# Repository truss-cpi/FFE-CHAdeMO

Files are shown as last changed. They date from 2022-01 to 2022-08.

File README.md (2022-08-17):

# FFE-CHAdeMO
Code and info for after-market CHAdeMO modifications to the Ford Focus Electric

The data provided has not been vetted or officially validated in any way. It is provided with no warranty and is used entirely at your own risk. 

High Voltage DC can easily maim or kill and should only be worked on by appropriately trained professionals.

You assume all responsibility if you damage anything or hurt/kill anyone using this code or information - and you agree that the creator of this repository will not be held liable in any way.

Remember: Not only will this kill you, it will hurt the whole time you're dying.

UPDATE:
A redesign of the control circuit is under way using parts that are more readily attainable and that do not require surface mount soldering. The ADM3052 is getting replaced by an MCP2561 High Speed CAN Transceiver, with SFH636 High Speed (1MBit) Optocouplers carrying the CAN0 Rx/Tx between the two isolated sections of the shield. These couplers are good for 2MHz switching frequency and the 500kbit data rate we're using should only need half that.

Validation is in progress with a "test" version of the shield code that can verify inputs/outputs, relay control and CAN transmission.

It should be noted that if the CAN1RX pin (DAC0) is not pulled up to 3.3V during validation testing, the CAN1TX pin (53) will not output test data reliably.

Also, the lowest CANBus data rate supported by the Arduino Due is 40kbit. Seen other lower values noted elsewhere but that seems to be the lowest value required by the CANBus spec and is the lowest that gave output when set on the Due.

New schematics to follow soon followed by a new board layout.

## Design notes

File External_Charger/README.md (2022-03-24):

The code in this folder controls a CHAdeMO Fast Charger interface, allowing multiple on-board charger modules (SOBDMs) to provide battery level DC output in parallel.

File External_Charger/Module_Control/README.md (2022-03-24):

This code generates CANBus frames that simulate module outputs the SOBDM expects to see during operation.

The module requires the vehicle to be in a specific state to go into charge mode and these data points are used to confirm that state.

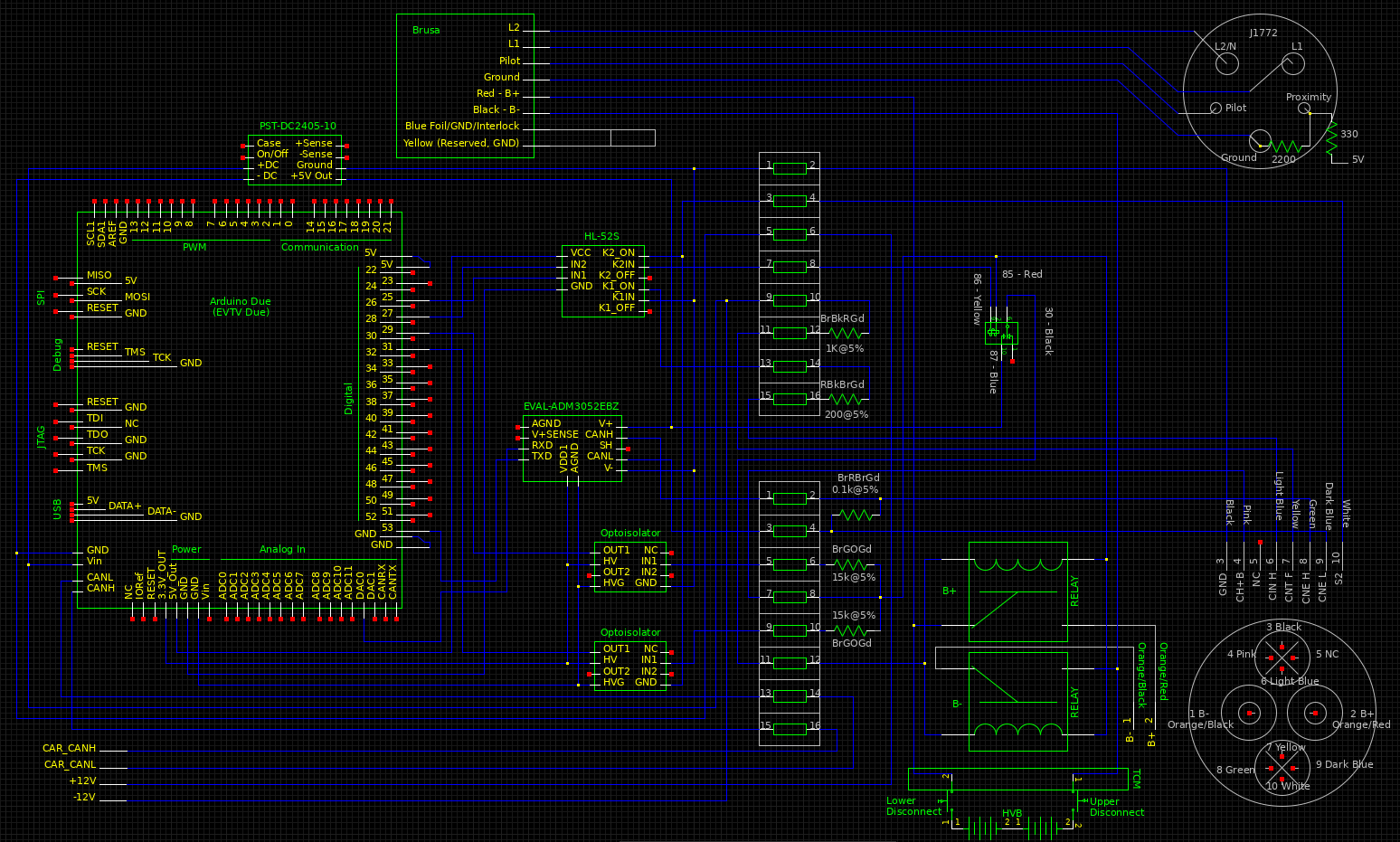
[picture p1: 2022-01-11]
Schematic Overview.png

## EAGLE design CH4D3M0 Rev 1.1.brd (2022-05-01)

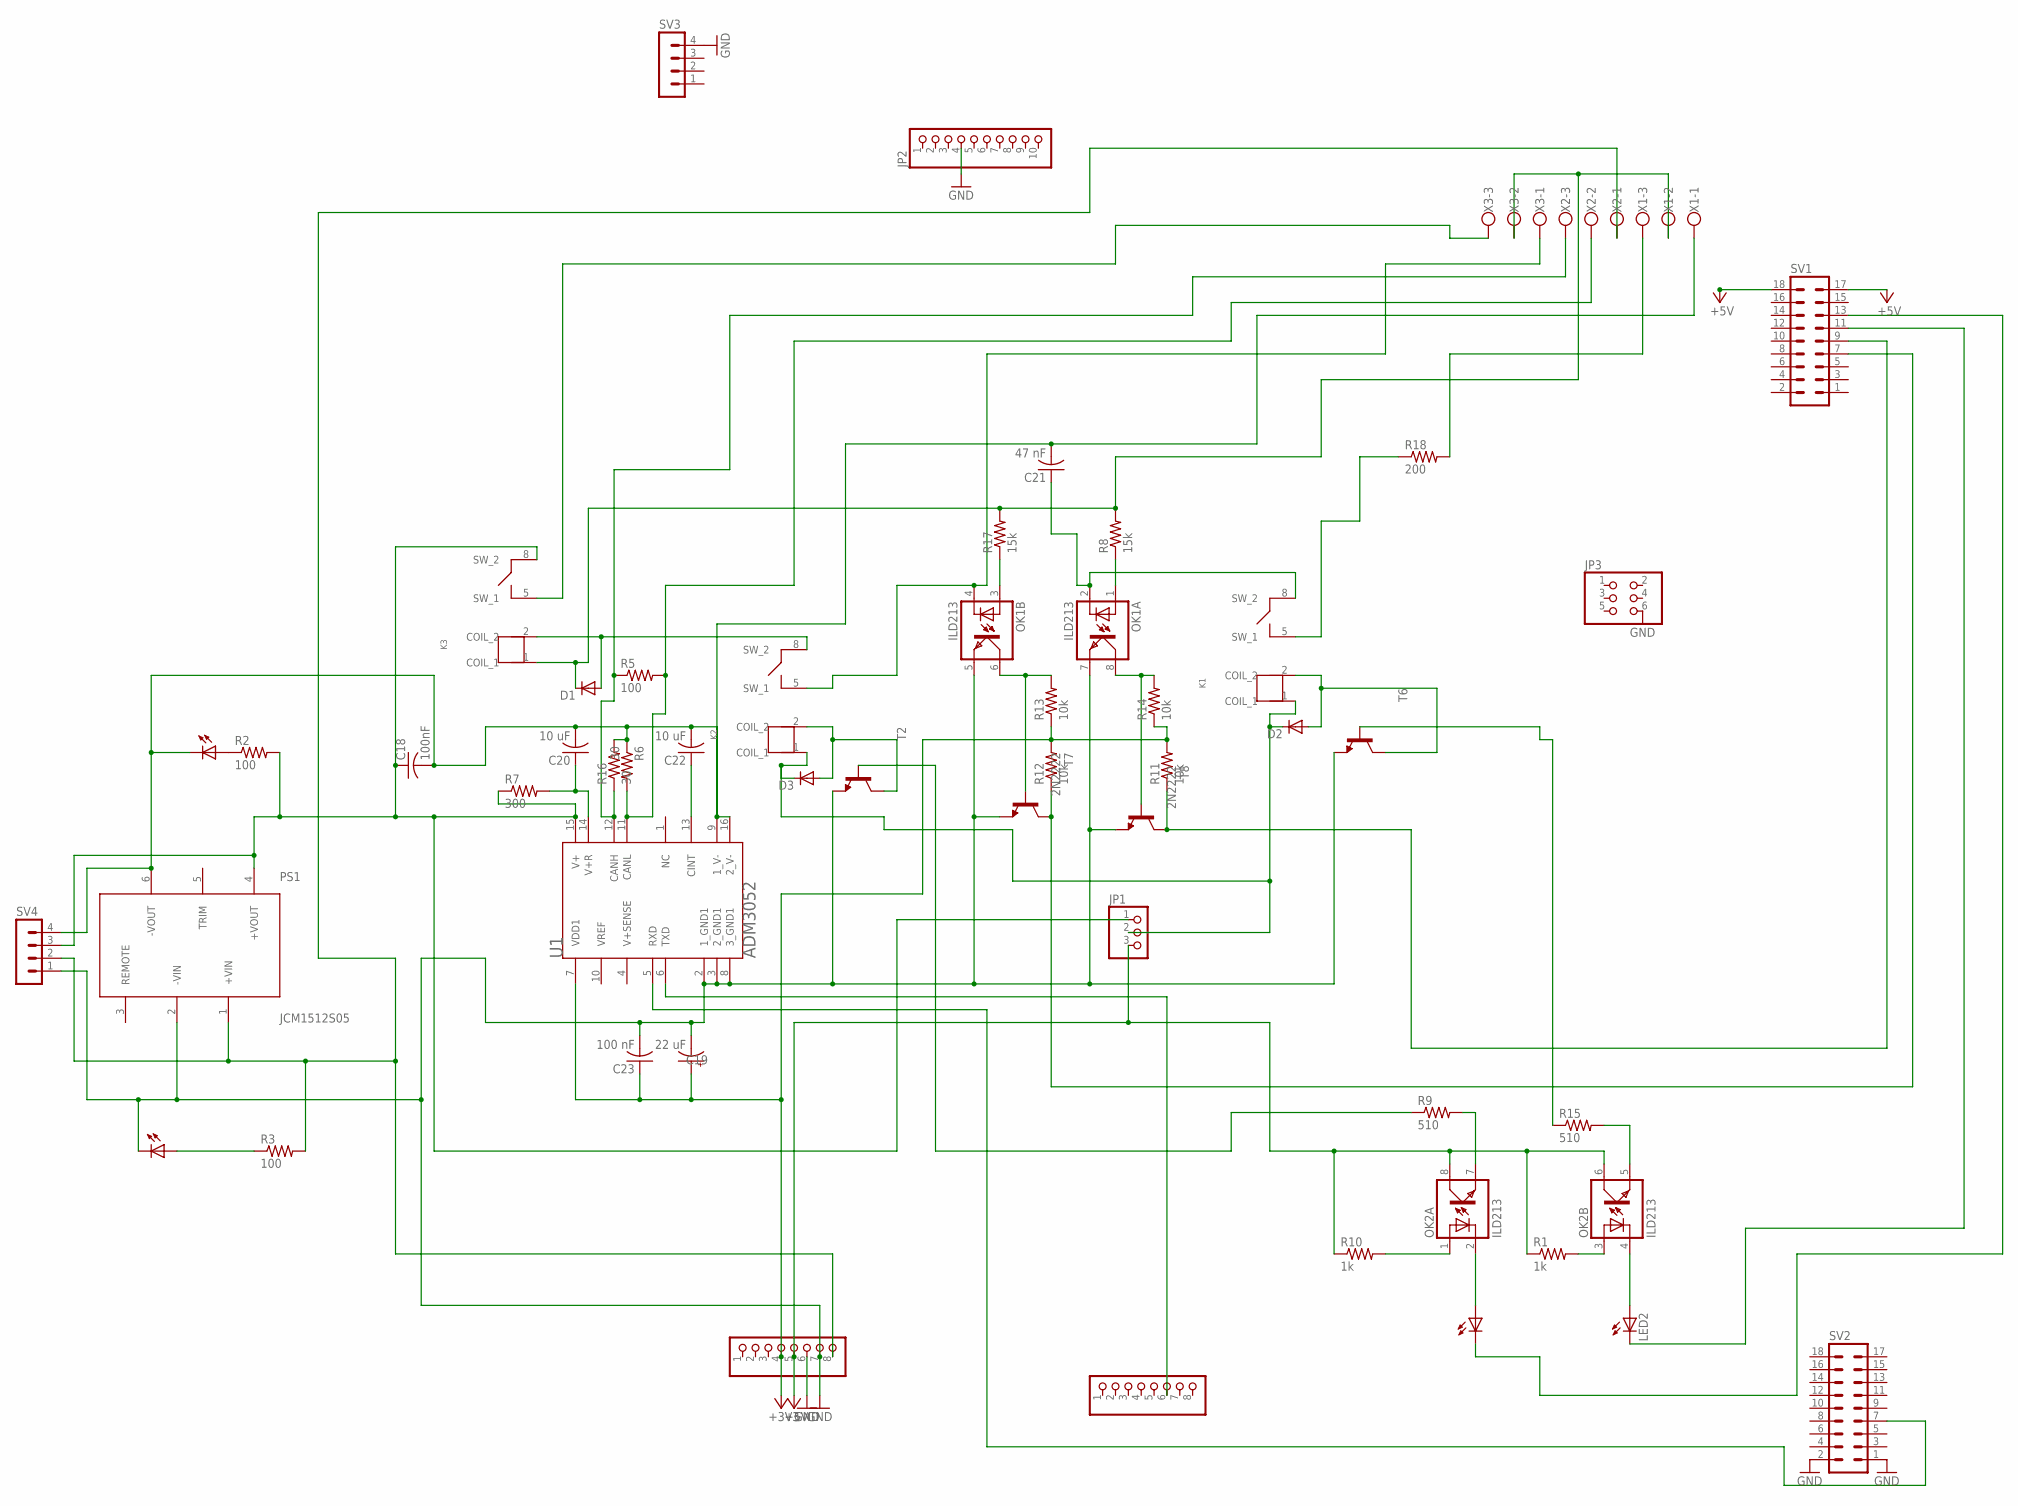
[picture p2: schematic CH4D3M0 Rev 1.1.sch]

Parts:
ADCH, ADCH2: PINHD-1X8; 1X08
C18: 100nF; C025-024X044
C19: 22 uF; E2,5RE
C20, C22: 10 uF; C025-024X044
C21: 47 nF; C025-024X044
C23: 100 nF; C025-024X044
D1, D2, D3: DIODE-D-5; D-5
JP1: PINHD-1X3; 1X03
JP2: PINHD-1X10; 1X10
JP3: PINHD-2X3; 2X03
K1, K2, K3: G6DN-1ATHROUGH_HOLE; G6DN-1A
LED1, LED2, LED3, LED4: LED_ELD260; LED_LD260
OK1, OK2: ILD213; SOIC08
PS1: JCM1512S05; JCMXX
R1, R10: 1k; 0204/7
R2, R3, R5: 100; 0204/7
R6, R16: 30; 0204/7
R7: 300; 0204/7
R8, R17: 15k; 0204/7
R9, R15: 510; 0204/7
R11, R12, R13, R14: 10k; 0204/7
R18: 200; 0204/7
SV1, SV2: MA09-2
SV3, SV4: MA04-1
T2, T6: BC547-NPN-TO92-CBE; TO92-CBE
T7, T8: 2N2222; TO92-EBC-OVAL
U1: ANALOG_DEVICES_INC_ADM3052ANALOG_DEVICES_INC_ADM3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; ANALOG_DEVICES_INC_ADM3052_0
X1, X2, X3: W237-103

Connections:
+3V3: ADCH2.4, C19.+, C23.1, R11.2, R12.2, R13.1, R14.1, U1.7 (VDD1)
+5V: ADCH2.5, JP1.3, OK2.6 (COL), OK2.8 (COL), R1.1, R10.1, SV1.17, SV1.18
GND: ADCH2.6, ADCH2.7, C19.-, C23.2, JP2.4, JP3.6, LED4.K (C), OK1.5 (EMIT), OK1.7 (EMIT), PS1.2 (-VIN), SV2.1, SV2.2, SV3.4, SV4.1, T2.E, T6.E, T7.E, T8.E, U1.2 (1_GND1), U1.3 (2_GND1), U1.8 (3_GND1)
unnamed: D2.C, D3.C, JP1.2, K1.1 (COIL_1), K2.1 (COIL_1)
unnamed: C18.1, JP1.1, K3.8 (SW_2), PS1.4 (+VOUT), R2.2, R7.1, SV4.3, U1.15 (V+)
unnamed: C20.1, R7.2, U1.14 (V+R)
unnamed: C22.1, U1.13 (CINT)
unnamed: K3.5 (SW_1), X3.3
unnamed: R18.2, X1.3
unnamed: C18.2, C20.2, C21.2, C22.2, LED3.K (C), PS1.6 (-VOUT), R6.1, R16.2, SV4.4, U1.9 (1_V-), U1.16 (2_V-), X1.1
unnamed: R5.2, R6.2, U1.11 (CANL), X2.2
unnamed: C21.1, K1.8 (SW_2), OK1.2 (C)
unnamed: K1.5 (SW_1), R18.1
unnamed: D1.C, K3.1 (COIL_1), R8.2, R17.2, X1.2, X3.2
unnamed: OK1.1 (A), R8.1
unnamed: OK1.3 (A), R17.1
unnamed: ADCH2.8, PS1.1 (+VIN), R3.2, SV4.2, X2.1
unnamed: D1.A, K2.8 (SW_2), K3.2 (COIL_2)
unnamed: K2.5 (SW_1), OK1.4 (C), X3.1
unnamed: OK1.6 (COL), R13.2, T7.B
unnamed: OK1.8 (COL), R14.2, T8.B
unnamed: R12.1, SV1.7, T7.C
unnamed: ADCH.6, U1.6 (TXD)
unnamed: R11.1, SV1.9, T8.C
unnamed: SV2.7, U1.5 (RXD)
unnamed: D2.A, K1.2 (COIL_2), T6.C
unnamed: D3.A, K2.2 (COIL_2), T2.C
unnamed: OK2.7 (EMIT), R9.2
unnamed: LED1.A, OK2.2 (C)
unnamed: OK2.1 (A), R10.2
unnamed: OK2.3 (A), R1.2
unnamed: R9.1, T2.B
unnamed: LED1.K (C), SV1.13
unnamed: R15.1, T6.B
unnamed: OK2.5 (EMIT), R15.2
unnamed: LED2.A, OK2.4 (C)
unnamed: LED2.K (C), SV1.11
unnamed: R5.1, R16.1, U1.12 (CANH), X2.3
unnamed: LED3.A, R2.1
unnamed: LED4.A, R3.1

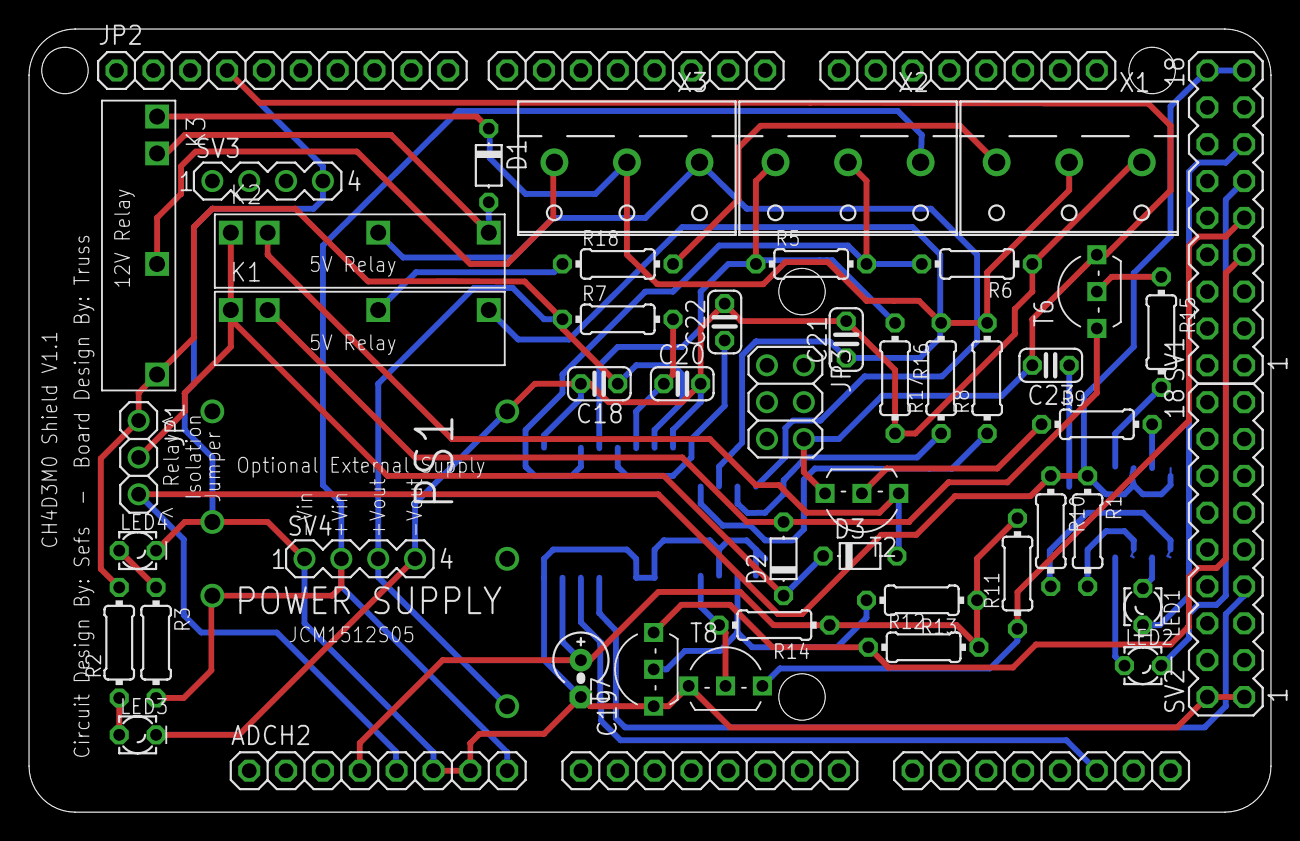
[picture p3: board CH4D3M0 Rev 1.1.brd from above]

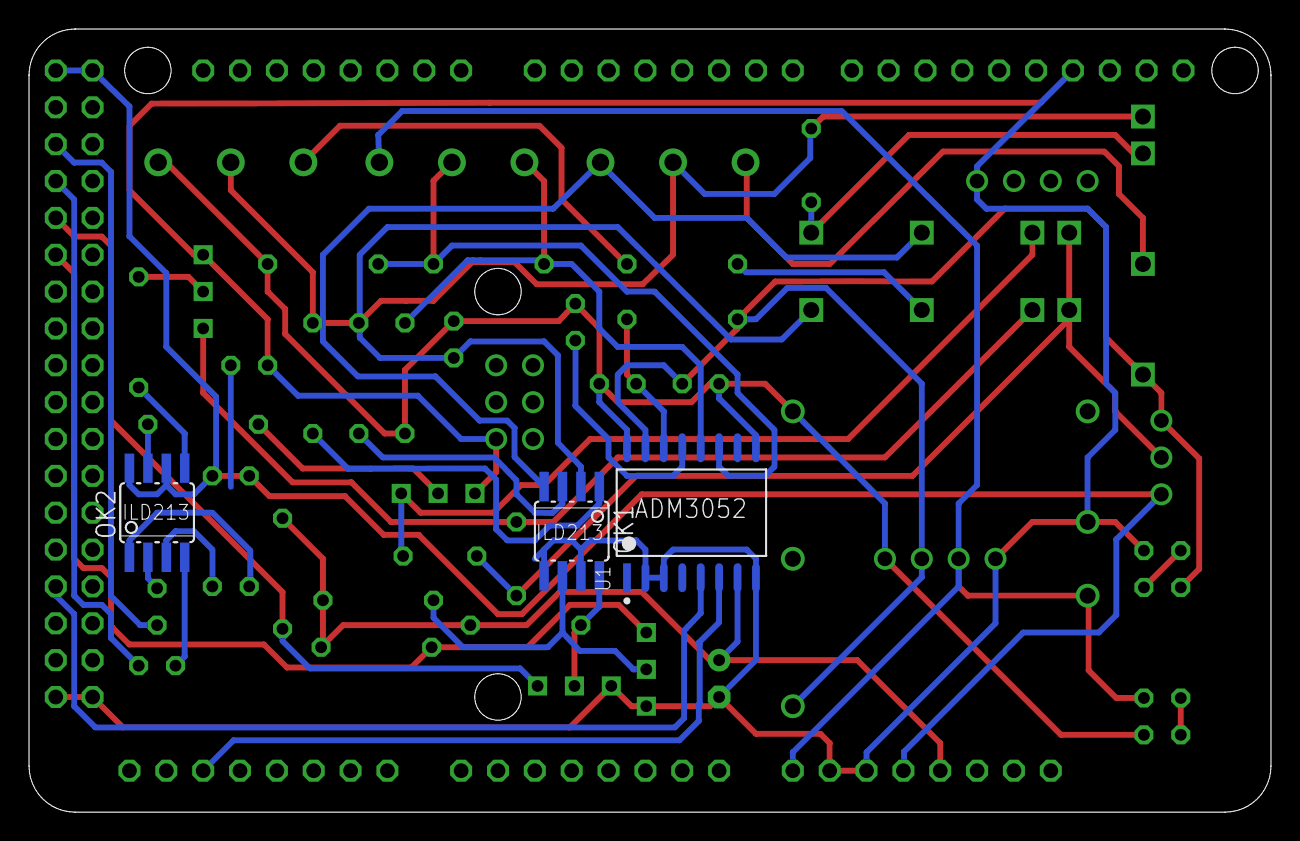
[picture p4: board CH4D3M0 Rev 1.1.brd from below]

Board: 2 copper layers, 85.6 x 54.0 mm, 56 parts (3 on the bottom side), 40 nets.

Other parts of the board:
ADCL: 1X08
COMMUNICATION: 1X08
PWML: 1X08

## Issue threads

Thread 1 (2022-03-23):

Sorry I'm didn't know where I can text you either...

Elan-II, 2022-03-23:
Last half year I'm looking for way to start ford fusion/focus/c-max electric on board 3.3 kWt charger, but I'm have only charger, not entire car. I'm working on EV conversion and repair service, and would like to ask some of your can logs, become you somehow find that 0x7E2 asks charger some status. I can give you al information about other chargers, that I'm turn on instead, if needed this.

Elan-II, 2022-03-23:
Because, not become...

Elan-II, 2022-03-24:
Can you give me link where you get that original code?

truss-cpi, 2022-03-24:
There is no original link. This was pursued as a personal project by the original author and the software was given to me when I purchased the hardware - as he did not wish to pursue development of it. I've posted it as open source so that others may use it. What you see IS the original code, with the exception of me cleaning up some formatting and adding more verbose comments.

There is other separate code I have not had a chance to look at that was used to control SOBDMs outside the vehicle, so they could be "stacked" together to act as a fast charger. There may be something of use in there. I'll try to get it posted to the main branch soon.

truss-cpi, 2022-03-24:
[https://github.com/truss-cpi/FFE-CHAdeMO/blob/main/External_Charger/Module_Control/sodbm_controller.ino](https://github.com/truss-cpi/FFE-CHAdeMO/blob/main/External_Charger/Module_Control/sodbm_controller.ino) should have what you're looking for. It has several loops that simulate the output of frames the SOBDM expects to see on the bus.

Elan-II, 2022-03-25:
As I'm see, it arduino project, can't you somehow add some strings like
Serial.print (received CAN id);
Serial.print (received CAN data[i];
And make some logs for me, while car chargings. I can pay you for this.

Closed 2022-03-24.

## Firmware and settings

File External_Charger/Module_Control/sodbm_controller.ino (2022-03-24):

#include <SPI.h>
#include <Arduino.h>
#include <due_can.h>
#include <due_wire.h>
#include "variant.h"
#include <Wire_EEPROM.h>
#include <Scheduler.h>
#include <elapsedMillis.h>

elapsedMillis timeElapsed;
elapsedMillis lrx;

#define Serial SerialUSB
template<class T> inline Print &operator <<(Print &obj, T arg) {
  obj.print(arg);  //Sets up Serial streaming Serial<<someshit;
  return obj;
}

class Field {
  public:
    uint16_t msb;
    uint16_t bits;
    uint32_t data;
    char* fieldName;
};

class Msg {
  public:
    char* moduleName;
    uint16_t msgID;
    uint64_t msg;
    Field fields[16];
    uint8_t field_count;
};

class StringTable {
  public:
    Msg messages[32];
};

class EEPROMvariables {
  public:
    uint8_t CANdo;        //Use Serial port if 2, CAN0 if 0 or CAN1 if 1
    char logfile[80];
    uint16_t transmitime = 0;
    boolean logger;
    uint32_t datarate = 500000;
    uint8_t goodEEPROM;
    CAN_FRAME outFrame;

};

StringTable stringTable;
EEPROMvariables myVars;
uint16_t page = 475;
uint16_t dummy;
char cmdBuffer[100];
char logstring[200];
char logstring2[300] = "";
char logstringt[200];
char logstringtl[200];
char logstringt1[200];
char logstringc1[200];
char logstringts[200];
char msgBuff[100];
float Version = 1.10;
int ptrBuffer;
short logcycle = 0;
boolean handlingEvent, debug;
int b1167 = 0x70;
int b142D = 0x02;
int reportedvolts = 0;
int reportedvoltspre = 0;
int tempA = 0;
int tempAint = 0;
int tempB = 0;
int tempBint = 0;
int tempC = 0;
int tempCint = 0;
int VACint = 0;
int AACint = 0;
int contcommand = 0;
float reportedamps = 0;
int VACint1 = 0;
int VACint2 = 0;
int reportvolts1 = 0;
int reportvolts2 = 0;
unsigned int timeout = 1000;

unsigned int incra = 1048575;
int chargevolts = 0;
float chargeamps = 0;
float battvolts = 333;
int chargevoltsint1 = 0;
int chargevoltsint2 = 0;
int chargecontrolint6 = 0;
int chargecontrolint7 = 0;
int chargeampsint = 0;
int battvoltsint = 0;
int reportedampsint = 0;



float acc = 0;
float pilot = 0;
float ampacity = 0;
float VAC = 0;
float AAC = 0;
float Hz = 0;
int sodbmdiagcycle = 1;
boolean sodbmreset = false;
int sodbmtoggle = 1;
int b207A = 0;
int b307A = 0;
int chargingstate=0;
int chargerStatus = 0;

CAN_FRAME inFrame;

void setup() {

  Wire.begin();
  Serial.begin(115200);

  EEPROM.setWPPin(19);
  EEPROM.read(page, myVars);
  if (myVars.goodEEPROM != 200)defaults();
  myVars.logger = false;


  initializeCAN();




  Scheduler.startLoop(ActiveDiagLoop);
  Scheduler.startLoop(StaticSimulatorLoop100ms);
  Scheduler.startLoop(StaticSimulatorLoop50ms);
  Scheduler.startLoop(StaticSimulatorLoop40ms);
  Scheduler.startLoop(OdometerSimulatorLoop);
  Scheduler.startLoop(GearShiftSimulatorLoop);
  Scheduler.startLoop(BECMStatusLoop);
  Scheduler.startLoop(SODBMControlLoop);
  Scheduler.startLoop(BECMVoltageLoop);
  Scheduler.startLoop(SysTimeSimulatorLoop);
  
  



}



void loop()
{
  while (SerialUSB.available()) {
    serialEvent();
  }
  sprintf(logstringtl, "%02X%02X", chargevoltsint1, chargevoltsint2);
  chargevolts = (float)strtol(logstringtl, NULL, 16);
  Serial<<"CV = ";
  Serial<<chargevolts;
  Serial<<" V          CC = ";
  Serial<<chargeampsint;
  Serial<<" A          Batt = ";
  Serial<<battvolts;
  Serial<<" V          AmpsOut = "; 
  Serial<<reportedamps;
  Serial<<" A          State = ";
  Serial<<chargingstate;
  Serial<<"\n"; 
  Serial<<"TempA = ";
  Serial<<tempA;
  Serial<<"     TempB = ";
  Serial<<tempB;
  Serial<<"     Temp C = ";
  Serial<<tempC;
  Serial<<"     Status = ";
  Serial<<chargerStatus;
  Serial<<"\n";
  
      reportedvolts = (reportedvoltspre & 0x1FF);
      reportedvolts = reportedvolts * 2;
      battvolts = reportedvolts/2;
      b207A = (reportedvolts & 0xFF00);
      b207A = b207A >> 8;
      b307A = (reportedvolts & 0x00FF);
    if (timeElapsed > timeout)
    {
      b1167 = 0x70;
      b142D = 0x02;
      chargingstate=0;
      chargeampsint = 0x00;
      chargevoltsint1 = 0x00;
      chargevoltsint2 = 0x00;
      chargecontrolint6 = 0x00;
      chargecontrolint7 = 0x00;
      contcommand = 0;
    }
    
    if (lrx > timeout)
    {
      pilot = 0;
        AAC = 0;
        VAC = 0;
        ampacity = 0;
        Hz = 0;
        tempAint = 0;
        tempA = 0;
        tempBint = 0;
        tempB = 0;
        tempCint = 0;
        tempC = 0;
    }


    myVars.outFrame.id = 0x105;
    myVars.outFrame.data.bytes[0] = reportvolts1;
    myVars.outFrame.data.bytes[1] = reportvolts2;
    myVars.outFrame.data.bytes[2] = reportedampsint;
    myVars.outFrame.data.bytes[3] = 0x00;
    myVars.outFrame.data.bytes[4] = 0x00;
    myVars.outFrame.data.bytes[5] = 0x00;
    myVars.outFrame.data.bytes[6] = 0x00;
    myVars.outFrame.data.bytes[7] = chargerStatus;
    sendCAN(myVars.CANdo);
    delay(40);
    myVars.outFrame.id = 0x109;
    myVars.outFrame.data.bytes[0] = VACint1;
    myVars.outFrame.data.bytes[1] = VACint2;
    myVars.outFrame.data.bytes[2] = AACint;
    myVars.outFrame.data.bytes[3] = 0x00;
    myVars.outFrame.data.bytes[4] = 0x00;
    myVars.outFrame.data.bytes[5] = tempAint;
    myVars.outFrame.data.bytes[6] = tempBint;
    myVars.outFrame.data.bytes[7] = tempCint;
    sendCAN(myVars.CANdo);

  /*
  sprintf(logstring2, "%.2f;%.2f;%.2f;%.2f;%.2f;%.2f;%.2f;%.2f;%.2f;%.2f;%.2f;%.2f;%.2f;%.2f;%.2f;%.2f;%.2f;%.2f;%.2f;%.2f;%.2f;%.2f;%.2f;%.2f;%.2f;%.2f;\n",
          batchadspl, hbattchar, hbattcoolin, mcon, hbattcurr, hbattvolt, ETE, hbatttemp, seqf,
          chacurrentf, torquedelivered, brakemode, estchatimef, motorRPM, MPH, throttle, brake, pwrt, acc, hvac, VAC, AAC, ampacity, Hz, mincell, maxcell);
  Serial << logstring2;
*/
  delay(60);
}

void ActiveDiagLoop()
{
  if (sodbmreset == true)
  {
    myVars.outFrame.id = 0x7E2;
    myVars.outFrame.data.bytes[0] = 0x04;
    myVars.outFrame.data.bytes[1] = 0x14;
    myVars.outFrame.data.bytes[2] = 0xFF;
    myVars.outFrame.data.bytes[3] = 0xFF;
    myVars.outFrame.data.bytes[4] = 0xFF;
    myVars.outFrame.data.bytes[5] = 0x00;
    myVars.outFrame.data.bytes[6] = 0x00;
    myVars.outFrame.data.bytes[7] = 0x00;
    myVars.outFrame.length = 8;
    myVars.outFrame.fid = 0;
    myVars.outFrame.rtr = 1;
    myVars.outFrame.priority = 0;
    myVars.outFrame.extended = false;
    Can0.sendFrame(myVars.outFrame);
  }




  sodbmdiagcycle =  sodbmdiagcycle * sodbmtoggle;

  if (sodbmdiagcycle == 1)
  {
    //SODBM Diagnostic Request for AC Voltage
    myVars.outFrame.id = 0x7E2;
    myVars.outFrame.data.bytes[0] = 0x03;
    myVars.outFrame.data.bytes[1] = 0x22;
    myVars.outFrame.data.bytes[2] = 0x48;
    myVars.outFrame.data.bytes[3] = 0x5E;
    myVars.outFrame.data.bytes[4] = 0x00;
    myVars.outFrame.data.bytes[5] = 0x00;
    myVars.outFrame.data.bytes[6] = 0x00;
    myVars.outFrame.data.bytes[7] = 0x00;
    myVars.outFrame.length = 8;
    myVars.outFrame.fid = 0;
    myVars.outFrame.rtr = 1;
    myVars.outFrame.priority = 0;
    myVars.outFrame.extended = false;
    Can0.sendFrame(myVars.outFrame);

  }

  else if (sodbmdiagcycle == 2)
  {
    //SODBM Diagnostic Request for AC Amps
    myVars.outFrame.id = 0x7E2;
    myVars.outFrame.data.bytes[0] = 0x03;
    myVars.outFrame.data.bytes[1] = 0x22;
    myVars.outFrame.data.bytes[2] = 0x48;
    myVars.outFrame.data.bytes[3] = 0x5F;
    myVars.outFrame.data.bytes[4] = 0x00;
    myVars.outFrame.data.bytes[5] = 0x00;
    myVars.outFrame.data.bytes[6] = 0x00;
    myVars.outFrame.data.bytes[7] = 0x00;
    myVars.outFrame.length = 8;
    myVars.outFrame.fid = 0;
    myVars.outFrame.rtr = 1;
    myVars.outFrame.priority = 0;
    myVars.outFrame.extended = false;
    Can0.sendFrame(myVars.outFrame);

  }

  else if (sodbmdiagcycle == 3)
  {
    //SODBM Diagnostic Request for Temp A
    myVars.outFrame.id = 0x7E2;
    myVars.outFrame.data.bytes[0] = 0x03;
    myVars.outFrame.data.bytes[1] = 0x22;
    myVars.outFrame.data.bytes[2] = 0xD1;
    myVars.outFrame.data.bytes[3] = 0x17;
    myVars.outFrame.data.bytes[4] = 0x00;
    myVars.outFrame.data.bytes[5] = 0x00;
    myVars.outFrame.data.bytes[6] = 0x00;
    myVars.outFrame.data.bytes[7] = 0x00;
    myVars.outFrame.length = 8;
    myVars.outFrame.fid = 0;
    myVars.outFrame.rtr = 1;
    myVars.outFrame.priority = 0;
    myVars.outFrame.extended = false;
    Can0.sendFrame(myVars.outFrame);

  }

  else if (sodbmdiagcycle == 4)
  {
    //SODBM Diagnostic Request for Temp B
    myVars.outFrame.id = 0x7E2;
    myVars.outFrame.data.bytes[0] = 0x03;
    myVars.outFrame.data.bytes[1] = 0x22;
    myVars.outFrame.data.bytes[2] = 0xD0;
    myVars.outFrame.data.bytes[3] = 0x0B;
    myVars.outFrame.data.bytes[4] = 0x00;
    myVars.outFrame.data.bytes[5] = 0x00;
    myVars.outFrame.data.bytes[6] = 0x00;
    myVars.outFrame.data.bytes[7] = 0x00;
    myVars.outFrame.length = 8;
    myVars.outFrame.fid = 0;
    myVars.outFrame.rtr = 1;
    myVars.outFrame.priority = 0;
    myVars.outFrame.extended = false;
    Can0.sendFrame(myVars.outFrame);

  }
  
    else if (sodbmdiagcycle == 5)
  {
    //SODBM Diagnostic Request for Temp C
    myVars.outFrame.id = 0x7E2;
    myVars.outFrame.data.bytes[0] = 0x03;
    myVars.outFrame.data.bytes[1] = 0x22;
    myVars.outFrame.data.bytes[2] = 0xD0;
    myVars.outFrame.data.bytes[3] = 0x0C;
    myVars.outFrame.data.bytes[4] = 0x00;
    myVars.outFrame.data.bytes[5] = 0x00;
    myVars.outFrame.data.bytes[6] = 0x00;
    myVars.outFrame.data.bytes[7] = 0x00;
    myVars.outFrame.length = 8;
    myVars.outFrame.fid = 0;
    myVars.outFrame.rtr = 1;
    myVars.outFrame.priority = 0;
    myVars.outFrame.extended = false;
    Can0.sendFrame(myVars.outFrame);

  }
  
  else if (sodbmdiagcycle == 6)
  {
    //SODBM Diagnostic Request for Status
    myVars.outFrame.id = 0x7E2;
    myVars.outFrame.data.bytes[0] = 0x03;
    myVars.outFrame.data.bytes[1] = 0x22;
    myVars.outFrame.data.bytes[2] = 0x48;
    myVars.outFrame.data.bytes[3] = 0x4F;
    myVars.outFrame.data.bytes[4] = 0x00;
    myVars.outFrame.data.bytes[5] = 0x00;
    myVars.outFrame.data.bytes[6] = 0x00;
    myVars.outFrame.data.bytes[7] = 0x00;
    myVars.outFrame.length = 8;
    myVars.outFrame.fid = 0;
    myVars.outFrame.rtr = 1;
    myVars.outFrame.priority = 0;
    myVars.outFrame.extended = false;
    Can0.sendFrame(myVars.outFrame);

  }
  delay(30);
}

void StaticSimulatorLoop100ms()
{
    //Exterior Temperature Message (100 ms)
    myVars.outFrame.id = 0x178;
    myVars.outFrame.data.bytes[0] = 0xC1;
    myVars.outFrame.data.bytes[1] = 0x2D;
    myVars.outFrame.data.bytes[2] = 0x00;
    myVars.outFrame.data.bytes[3] = 0x00;
    myVars.outFrame.data.bytes[4] = 0x8E;
    myVars.outFrame.data.bytes[5] = 0x4D;
    myVars.outFrame.data.bytes[6] = 0xB6;
    myVars.outFrame.data.bytes[7] = 0x4D;
    myVars.outFrame.length = 8;
    myVars.outFrame.fid = 0;
    myVars.outFrame.rtr = 1;
    myVars.outFrame.priority = 0;
    myVars.outFrame.extended = false;
    Can0.sendFrame(myVars.outFrame);
    
    delay(45);
    
    //Charger's DC/DC converter command Disable (100 ms)
    myVars.outFrame.id = 0x42D;
    myVars.outFrame.data.bytes[0] = 0x00;
    myVars.outFrame.data.bytes[1] = b142D; //0x02 before charge, 0x42 on charge
    myVars.outFrame.data.bytes[2] = 0x4D;
    myVars.outFrame.data.bytes[3] = 0x00;
    myVars.outFrame.data.bytes[4] = 0x46;
    myVars.outFrame.data.bytes[5] = 0x00;
    myVars.outFrame.data.bytes[6] = 0x00;
    myVars.outFrame.data.bytes[7] = 0x00;
    myVars.outFrame.length = 8;
    myVars.outFrame.fid = 0;
    myVars.outFrame.rtr = 1;
    myVars.outFrame.priority = 0;
    myVars.outFrame.extended = false;
    Can0.sendFrame(myVars.outFrame);
    delay(45);
}


void StaticSimulatorLoop50ms()
{
    //DC/DC Converter Low Voltage Set Point (50 ms)
    myVars.outFrame.id = 0x43E;
    myVars.outFrame.data.bytes[0] = 0x00;
    myVars.outFrame.data.bytes[1] = 0xA1;
    myVars.outFrame.data.bytes[2] = 0x00;
    myVars.outFrame.data.bytes[3] = 0x00;
    myVars.outFrame.data.bytes[4] = 0x00;
    myVars.outFrame.data.bytes[5] = 0x00;
    myVars.outFrame.data.bytes[6] = 0x00;
    myVars.outFrame.data.bytes[7] = 0x00;
    myVars.outFrame.length = 8;
    myVars.outFrame.fid = 0;
    myVars.outFrame.rtr = 1;
    myVars.outFrame.priority = 0;
    myVars.outFrame.extended = false;
    Can0.sendFrame(myVars.outFrame);
    delay(13);
    
    //DC/DC Converter Main Status (50 ms)
    myVars.outFrame.id = 0x43D;
    myVars.outFrame.data.bytes[0] = 0x43;
    myVars.outFrame.data.bytes[1] = 0x0F;
    myVars.outFrame.data.bytes[2] = 0x91;
    myVars.outFrame.data.bytes[3] = 0x19;
    myVars.outFrame.data.bytes[4] = 0x08;
    myVars.outFrame.data.bytes[5] = 0x94;
    myVars.outFrame.data.bytes[6] = 0x02;
    myVars.outFrame.data.bytes[7] = 0xA9;
    myVars.outFrame.length = 8;
    myVars.outFrame.fid = 0;
    myVars.outFrame.rtr = 1;
    myVars.outFrame.priority = 0;
    myVars.outFrame.extended = false;
    Can0.sendFrame(myVars.outFrame);
    delay(13);
    
    //Some PCM/ECM BS (50 ms)
    myVars.outFrame.id = 0x43E;
    myVars.outFrame.data.bytes[0] = 0x00;
    myVars.outFrame.data.bytes[1] = 0xA1;
    myVars.outFrame.data.bytes[2] = 0x00;
    myVars.outFrame.data.bytes[3] = 0x00;
    myVars.outFrame.data.bytes[4] = 0x00;
    myVars.outFrame.data.bytes[5] = 0x00;
    myVars.outFrame.data.bytes[6] = 0x00;
    myVars.outFrame.data.bytes[7] = 0x00;
    myVars.outFrame.length = 8;
    myVars.outFrame.fid = 0;
    myVars.outFrame.rtr = 1;
    myVars.outFrame.priority = 0;
    myVars.outFrame.extended = false;
    Can0.sendFrame(myVars.outFrame);
    delay(13);
}


void StaticSimulatorLoop40ms()
{
  //Main ECU Voltage Supply (40 ms)
    myVars.outFrame.id = 0x242;
    myVars.outFrame.data.bytes[0] = 0x04;//static
    myVars.outFrame.data.bytes[1] = 0xD0;//static
    myVars.outFrame.data.bytes[2] = 0x20;//static
    myVars.outFrame.data.bytes[3] = 0x0C;//static
    myVars.outFrame.data.bytes[4] = 0xE9;//static
    myVars.outFrame.data.bytes[5] = 0x28;
    myVars.outFrame.data.bytes[6] = 0x04;
    myVars.outFrame.data.bytes[7] = 0x01;
    myVars.outFrame.length = 8;
    myVars.outFrame.fid = 0;
    myVars.outFrame.rtr = 1;
    myVars.outFrame.priority = 0;
    myVars.outFrame.extended = false;
    Can0.sendFrame(myVars.outFrame);
    delay(35);
    
    myVars.outFrame.id = 0x242;
    myVars.outFrame.data.bytes[0] = 0x04;//static
    myVars.outFrame.data.bytes[1] = 0xD0;//static
    myVars.outFrame.data.bytes[2] = 0x20;//static
    myVars.outFrame.data.bytes[3] = 0x0C;//static
    myVars.outFrame.data.bytes[4] = 0xE9;//static
    myVars.outFrame.data.bytes[5] = 0x28;
    myVars.outFrame.data.bytes[6] = 0x00;
    myVars.outFrame.data.bytes[7] = 0x00;
    myVars.outFrame.length = 8;
    myVars.outFrame.fid = 0;
    myVars.outFrame.rtr = 1;
    myVars.outFrame.priority = 0;
    myVars.outFrame.extended = false;
    Can0.sendFrame(myVars.outFrame);
    delay(35);
    
    myVars.outFrame.id = 0x242;
    myVars.outFrame.data.bytes[0] = 0x04;//static
    myVars.outFrame.data.bytes[1] = 0xD0;//static
    myVars.outFrame.data.bytes[2] = 0x20;//static
    myVars.outFrame.data.bytes[3] = 0x0C;//static
    myVars.outFrame.data.bytes[4] = 0xE9;//static
    myVars.outFrame.data.bytes[5] = 0x2C;
    myVars.outFrame.data.bytes[6] = 0x05;
    myVars.outFrame.data.bytes[7] = 0x01;
    myVars.outFrame.length = 8;
    myVars.outFrame.fid = 0;
    myVars.outFrame.rtr = 1;
    myVars.outFrame.priority = 0;
    myVars.outFrame.extended = false;
    Can0.sendFrame(myVars.outFrame);
    delay(35);
    
    myVars.outFrame.id = 0x242;
    myVars.outFrame.data.bytes[0] = 0x04;//static
    myVars.outFrame.data.bytes[1] = 0xD0;//static
    myVars.outFrame.data.bytes[2] = 0x20;//static
    myVars.outFrame.data.bytes[3] = 0x0C;//static
    myVars.outFrame.data.bytes[4] = 0xE9;//static
    myVars.outFrame.data.bytes[5] = 0x28;
    myVars.outFrame.data.bytes[6] = 0x00;
    myVars.outFrame.data.bytes[7] = 0x00;
    myVars.outFrame.length = 8;
    myVars.outFrame.fid = 0;
    myVars.outFrame.rtr = 1;
    myVars.outFrame.priority = 0;
    myVars.outFrame.extended = false;
    Can0.sendFrame(myVars.outFrame);
    delay(35);
    
    myVars.outFrame.id = 0x242;
    myVars.outFrame.data.bytes[0] = 0x04;//static
    myVars.outFrame.data.bytes[1] = 0xD0;//static
    myVars.outFrame.data.bytes[2] = 0x20;//static
    myVars.outFrame.data.bytes[3] = 0x0C;//static
    myVars.outFrame.data.bytes[4] = 0xE9;//static
    myVars.outFrame.data.bytes[5] = 0x28;
    myVars.outFrame.data.bytes[6] = 0x04;
    myVars.outFrame.data.bytes[7] = 0x01;
    myVars.outFrame.length = 8;
    myVars.outFrame.fid = 0;
    myVars.outFrame.rtr = 1;
    myVars.outFrame.priority = 0;
    myVars.outFrame.extended = false;
    Can0.sendFrame(myVars.outFrame);
    delay(35);
    
    myVars.outFrame.id = 0x242;
    myVars.outFrame.data.bytes[0] = 0x04;//static
    myVars.outFrame.data.bytes[1] = 0xD0;//static
    myVars.outFrame.data.bytes[2] = 0x20;//static
    myVars.outFrame.data.bytes[3] = 0x0C;//static
    myVars.outFrame.data.bytes[4] = 0xE9;//static
    myVars.outFrame.data.bytes[5] = 0x2C;
    myVars.outFrame.data.bytes[6] = 0x02;
    myVars.outFrame.data.bytes[7] = 0x00;
    myVars.outFrame.length = 8;
    myVars.outFrame.fid = 0;
    myVars.outFrame.rtr = 1;
    myVars.outFrame.priority = 0;
    myVars.outFrame.extended = false;
    Can0.sendFrame(myVars.outFrame);
    delay(35);
    
    myVars.outFrame.id = 0x242;
    myVars.outFrame.data.bytes[0] = 0x04;//static
    myVars.outFrame.data.bytes[1] = 0xD0;//static
    myVars.outFrame.data.bytes[2] = 0x20;//static
    myVars.outFrame.data.bytes[3] = 0x0C;//static
    myVars.outFrame.data.bytes[4] = 0xE9;//static
    myVars.outFrame.data.bytes[5] = 0x28;
    myVars.outFrame.data.bytes[6] = 0x00;
    myVars.outFrame.data.bytes[7] = 0x00;
    myVars.outFrame.length = 8;
    myVars.outFrame.fid = 0;
    myVars.outFrame.rtr = 1;
    myVars.outFrame.priority = 0;
    myVars.outFrame.extended = false;
    Can0.sendFrame(myVars.outFrame);
    delay(35);
    
    myVars.outFrame.id = 0x242;
    myVars.outFrame.data.bytes[0] = 0x04;//static
    myVars.outFrame.data.bytes[1] = 0xD0;//static
    myVars.outFrame.data.bytes[2] = 0x20;//static
    myVars.outFrame.data.bytes[3] = 0x0C;//static
    myVars.outFrame.data.bytes[4] = 0xE9;//static
    myVars.outFrame.data.bytes[5] = 0x2C;
    myVars.outFrame.data.bytes[6] = 0x04;
    myVars.outFrame.data.bytes[7] = 0x01;
    myVars.outFrame.length = 8;
    myVars.outFrame.fid = 0;
    myVars.outFrame.rtr = 1;
    myVars.outFrame.priority = 0;
    myVars.outFrame.extended = false;
    Can0.sendFrame(myVars.outFrame);
    delay(35);
    
    myVars.outFrame.id = 0x242;
    myVars.outFrame.data.bytes[0] = 0x04;//static
    myVars.outFrame.data.bytes[1] = 0xD0;//static
    myVars.outFrame.data.bytes[2] = 0x20;//static
    myVars.outFrame.data.bytes[3] = 0x0C;//static
    myVars.outFrame.data.bytes[4] = 0xE9;//static
    myVars.outFrame.data.bytes[5] = 0x28;
    myVars.outFrame.data.bytes[6] = 0x00;
    myVars.outFrame.data.bytes[7] = 0x00;
    myVars.outFrame.length = 8;
    myVars.outFrame.fid = 0;
    myVars.outFrame.rtr = 1;
    myVars.outFrame.priority = 0;
    myVars.outFrame.extended = false;
    Can0.sendFrame(myVars.outFrame);
    delay(35);
    
    myVars.outFrame.id = 0x242;
    myVars.outFrame.data.bytes[0] = 0x04;//static
    myVars.outFrame.data.bytes[1] = 0xD0;//static
    myVars.outFrame.data.bytes[2] = 0x20;//static
    myVars.outFrame.data.bytes[3] = 0x0C;//static
    myVars.outFrame.data.bytes[4] = 0xE9;//static
    myVars.outFrame.data.bytes[5] = 0x28;
    myVars.outFrame.data.bytes[6] = 0x05;
    myVars.outFrame.data.bytes[7] = 0x01;
    myVars.outFrame.length = 8;
    myVars.outFrame.fid = 0;
    myVars.outFrame.rtr = 1;
    myVars.outFrame.priority = 0;
    myVars.outFrame.extended = false;
    Can0.sendFrame(myVars.outFrame);
    delay(35);
}
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

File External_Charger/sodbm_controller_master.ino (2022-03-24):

#include <SPI.h>
#include <Arduino.h>
#include <due_can.h>
#include <due_wire.h>
#include "variant.h"
#include <Wire_EEPROM.h>
#include <Scheduler.h>
#include <elapsedMillis.h>

elapsedMillis timeElapsed;
elapsedMillis v100lrx;
elapsedMillis v101lrx;
elapsedMillis v102lrx;

elapsedMillis mod1lrx;
elapsedMillis mod2lrx;
elapsedMillis mod3lrx;
elapsedMillis mod4lrx;
elapsedMillis mod5lrx;

#define Serial SerialUSB
template<class T> inline Print &operator <<(Print &obj, T arg) {
  obj.print(arg);  //Sets up Serial streaming Serial<<someshit;
  return obj;
}

class Field {
  public:
    uint16_t msb;
    uint16_t bits;
    uint32_t data;
    char* fieldName;
};

class Msg {
  public:
    char* moduleName;
    uint16_t msgID;
    uint64_t msg;
    Field fields[16];
    uint8_t field_count;
};

class StringTable {
  public:
    Msg messages[32];
};

class EEPROMvariables {
  public:
    uint8_t CANdo;        //Use Serial port if 2, CAN0 if 0 or CAN1 if 1
    char logfile[80];
    uint16_t transmitime = 0;
    boolean logger;
    uint32_t datarate = 500000;
    uint8_t goodEEPROM;
    CAN_FRAME outFrame;

};

StringTable stringTable;
EEPROMvariables myVars;
uint16_t page = 475;
uint16_t dummy;
char cmdBuffer[100];
char logstring[200];
char logstring2[300] = "";
char logstringt[200];
char logstringtl[200];
char logstringt1[200];
char logstringc1[200];
char logstringts[200];
char logstringveh[200];
char msgBuff[100];
float Version = 1.10;
int ptrBuffer;
short logcycle = 0;
boolean handlingEvent, debug;
int b1167 = 0x70;
int b142D = 0x02;
int reportedvolts = 0;
int reportedvoltspre = 0;
int tempA = 0;
int tempAint = 0;
int tempB = 0;
int tempBint = 0;
int tempC = 0;
int tempCint = 0;
int VACint = 0;
int AACint = 0;
int contcommand = 0;
boolean coolingfansmanual = false;
int tempincra = 0;
float contcommandfloat = 0;
float reportedamps = 0;
float mod1DCamps = 0;
float mod2DCamps = 0;
float mod3DCamps = 0;
float mod4DCamps = 0;
float mod5DCamps = 0;
float quickchargeamps = 0;
float mod1DCvolts = 0;
float mod2DCvolts = 0;
float mod3DCvolts = 0;
float mod4DCvolts = 0;
float mod5DCvolts = 0;
float mod1tempA = 0;
float mod1tempB = 0;
float mod1tempC = 0;
float mod2tempA = 0;
float mod2tempB = 0;
float mod2tempC = 0;
float mod3tempA = 0;
float mod3tempB = 0;
float mod3tempC = 0;
float mod4tempA = 0;
float mod4tempB = 0;
float mod4tempC = 0;
float mod5tempA = 0;
float mod5tempB = 0;
float mod5tempC = 0;
float mod1ACamps = 0;
float mod2ACamps = 0;
float mod3ACamps = 0;
float mod4ACamps = 0;
float mod5ACamps = 0;
float mod1ACvolts = 0;
float mod2ACvolts = 0;
float mod3ACvolts = 0;
float mod4ACvolts = 0;
float mod5ACvolts = 0;
boolean sodbmReset = false;
boolean moduleReset = true;
int resetincra = 0;
boolean chademoenable = false;
boolean coolingfansAenable = false;
boolean coolingfansBenable = false;
float coolingfansAenablefloat = 0;
float coolingfansBenablefloat = 0;
boolean coolingfansAauto = false;
boolean coolingfansBauto = false;




int j = 38;
boolean vehper = false;
int d1 = 22;
int d2 = 24;
int connectorpin = 26;
int contactor = 28;
int controllers = 30;
int chargingmodules = 32;
int coolingfansA = 34;
int coolingfansB = 36;


int vehmaxbattvolt = 0;
int SOCconstant = 0;
int maxchargetime10s = 0;
int maxchargetime1min = 0;
int estchargetime1min = 0;
float estchargetime1minfloat = 0;
int chargeseqcontrolnum = 0;
int vehtargetbattvolt = 0;
int vehcurrentreq = 0;
int vehfaultflag = 0;
boolean vfbattovolt = false;
boolean vfbattuvolt = false;
boolean vfbattcd = false;
boolean vfbatthtemp = false;
boolean vfbattvoltdev = false;
int vehstatusflag = 0;
boolean vehcharenable = false;
boolean vehpark = false;
boolean vehchafault = false;
boolean vehcontactor = true;
boolean vehnormstop = false;
int SOCdisplay = 0;
float SOCdisplayfloat = 0;
int chaseq = 0;
int incra = 0;
int chaloopstart = 0;
int incraDelta = 0;
unsigned int timeout = 1000;

boolean chastartstop = false;
float chastartstopfloat = 0;
boolean chacan = false;

int charavailoutputvolts = 0;
int charavailoutputvolts1 = 0;
int charavailoutputvolts2 = 0;
int charavailoutputcurr = 0;
int threshvolts = 0;
int threshvolts1 = 0;
int threshvolts2 = 0;
int charoutputvolts = 0;
int charoutputvolts1 = 0;
int charoutputvolts2 = 0;
int charoutputcurr = 0;
int charflagout = 0;
int charremaintime10s = 0;
int charremaintime1min = 0;
boolean charstatus = false;
boolean charmalfunct = false;
boolean charlock = false;
boolean charbattincomp = false;
boolean charsysmalfunct = false;
boolean charstopcontrol = false;
float sodbmResetfloat = 0;
float moduleResetfloat = 0;







int chargevolts = 0;
float chargevoltsfloat = 0;
float chargeamps = 0;
float battvolts = 333;
int chargevoltsint1 = 0;
int chargevoltsint2 = 0;
int chargecontrolint6 = 0;
int chargecontrolint7 = 0;
int chargeampsint = 0;
float chargeampsintfloat = 0;
int chargeampsint1 = 0;
int chargeampsint2 = 0;
int chargeampsint3 = 0;
int chargeampsint4 = 0;
int chargeampsint5 = 0;
int battvoltsint = 0;
int mod1chargerStatus = 0;
int mod2chargerStatus = 0;
int mod3chargerStatus = 0;
int mod4chargerStatus = 0;
int mod5chargerStatus = 0;
float mod1chargerStatusfloat = 0;
float mod2chargerStatusfloat = 0;
float mod3chargerStatusfloat = 0;
float mod4chargerStatusfloat = 0;
float mod5chargerStatusfloat = 0;



float acc = 0;
float pilot = 0;
float ampacity = 0;
float VAC = 0;
float AAC = 0;
float Hz = 0;
int sodbmdiagcycle = 1;
int sodbmtoggle = 1;
int b207A = 0;
int b307A = 0;
int chargingstate = 0;

CAN_FRAME inFrame;

void setup() {

  Wire.begin();
  Serial.begin(115200);

  EEPROM.setWPPin(19);
  EEPROM.read(page, myVars);
  if (myVars.goodEEPROM != 200)defaults();
  myVars.logger = false;


  initializeCAN();

  pinMode(j, INPUT_PULLUP);
  pinMode(d1, OUTPUT);
  pinMode(d2, OUTPUT);
  pinMode(connectorpin, OUTPUT);
  pinMode(contactor, OUTPUT);
  pinMode(controllers, OUTPUT);
  pinMode(chargingmodules, OUTPUT);
  pinMode(coolingfansA, OUTPUT);
  pinMode(coolingfansB, OUTPUT);

  digitalWrite(d1, HIGH);
  digitalWrite(d2, HIGH);
  digitalWrite(connectorpin, HIGH);
  digitalWrite(contactor, HIGH);
  digitalWrite(controllers, HIGH);
  digitalWrite(chargingmodules, HIGH);
  digitalWrite(coolingfansA, HIGH);
  digitalWrite(coolingfansB, HIGH);




  Scheduler.startLoop(ChademoLoop);
  Scheduler.startLoop(ControllerStartup);
  Scheduler.startLoop(temperatureLoop);

}

void ControllerStartup()
{
  if (moduleReset == true)
  {
    digitalWrite(controllers, HIGH);
    digitalWrite(chargingmodules, HIGH);
    delay(2000);
    digitalWrite(controllers, LOW);
    delay(2000);
    digitalWrite(chargingmodules, LOW);
    moduleReset = false;
  }
  delay(100);
}
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

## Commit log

2021-12-14 Update README.md
    Initial readme framework - I will not be held liable
2021-12-14 Add files via upload
    Vehicle-side Arduino code for managing CHAdeMO operation. Additional code included for serial-based monitoring/display app.
2022-01-11 Add files via upload
    This board and schematic should be examined before use - I am not a board designer and almost certainly run afoul of best practices.
    [CH4D3M0 Rev 1.brd, CH4D3M0 Rev 1.sch]
2022-01-11 Add files via upload
    Diagram of the original circuit
2022-01-18 Create Schematic Overview Details
2022-05-01 Rename CH4D3M0 Rev 1.brd to CH4D3M0 Rev 1.1.brd
    Updated schematic and board layout with snubber diode for 12V relay
    [CH4D3M0 Rev 1.1.brd]
2022-05-01 Rename CH4D3M0 Rev 1.sch to CH4D3M0 Rev 1.1.sch
    Updated schematic with snubber diode for 12V relay and corrected capacitor value(s)
    [CH4D3M0 Rev 1.1.sch]
2022-06-11 Update README.md
    Flaws in original board design have been found and are being reworked/tested
